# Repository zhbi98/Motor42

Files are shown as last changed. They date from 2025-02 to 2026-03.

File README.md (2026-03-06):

# Motor42

转速-扭矩特性步进电机运用普通的开环控制方式在低速和低负载的情况下可以保持较好的控制精度，但随着负载增大或转速度增加会发生丢步，另一个是转速-扭矩特性让步进电机无法在高转速下稳定工作。

## 特性

在低速状态下，步进电机的扭矩特性曲线通常为水平直线，能够提供较高的扭矩。在高速状态下，由于电感的影响，扭矩特性曲线呈指数下降，导致电机的负载能力显著降低。

> **最大扭矩：** 最大扭矩出现在中低转速范围，随着转速的提高，扭矩会逐渐下降。因为在高频率下，电流流动受到绕组电感的影响，导致电流无法达到稳定值，从而扭矩降低。
> 
> **启动扭矩与连续扭矩：** 启动扭矩指在启动时能够提供的最大扭矩，而连续扭矩则指电机持续运行时能够维持的扭矩。随着脉冲频率的增加，启动扭矩和连续扭矩都会下降。

## 闭环

闭环控制是在开环控制的基础上，增加了 **反馈检测环节**（例如在电机轴增加编码器），形成指令-执行-位置检测-修正的闭环逻辑。解决存在的丢步、偏差、抗干扰能力弱问题，还能提升系统和容错能力。

## FOC 控制

混合式步进电机与无刷电机的内在联系（结构定义相似性，工作原理相似性），所以可以用无刷电机 FOC 的驱动思想驱动步进电机。

结构方面：永磁转子+定子绕组的结构，定子方面：两者都有多相绕组（步进电机通常为两相，无刷电机通常为三相），转子方面：都采用永磁材料制造转子磁极，无刷设计：两者都没有电刷和机械换向器，依靠电子换向。

对于两相步进电机，虽然只有两个绕组，但通常两相绕组是正交的，从而可以简化步骤，省略我们的 clarke 变换，所以其余同样可以采用类似的思路进行一个电流环FOC控制。

    电流检测：对 AB 两相电流进行检测
    Park变换：将 AB 轴静止系转换为dq轴旋转坐标系
    PI调节器：对 Id 和 Iq 进行控制
    Invpark变换：讲 dq 轴转换为AB轴
    SVPWM调制: 输出占空比
    双 H桥驱动：驱动我们的步进电机

这些可以整合到一个驱动器中实现，如下图。这就是一体化集成步进电机闭环驱动器。板上集成磁编码器，具有速度，位置，电流闭环控制功能，适用于 3D 打印机，小型机械臂。

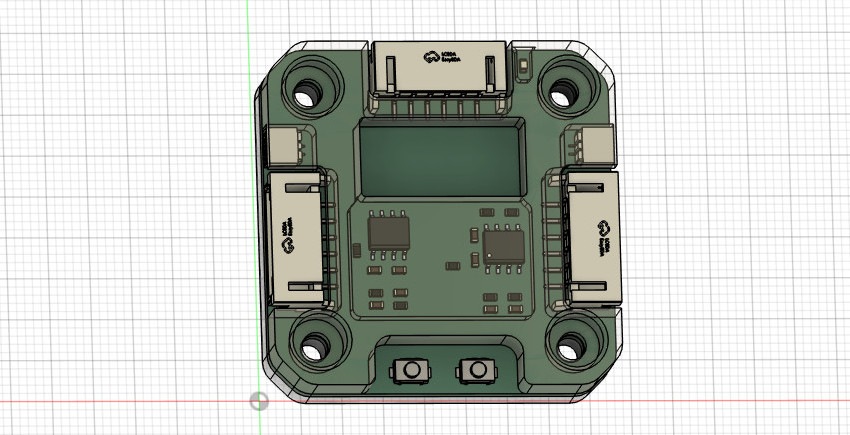
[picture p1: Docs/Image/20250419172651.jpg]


## 硬件

(1) 2 相逆变功率级：东芝凌耐压 50V，载流3.5A 的 PWM 斩波式双全桥电机驱动器，内置带低导通电阻的输出MOSFET（基于成本考虑可以选择其他的型号）。

(2) RS485 收发器：TI 德州仪器 SN75176B（基于成本考虑可以选择其他的型号）。

(3) CAN2.0B 收发器：NXP 恩智浦 High-speed CAN transceiver TJA1051（基于成本考虑可以选择其他的型号）。

(4) 磁编码器：MagnTek 麦歌恩 mt6816 单圈绝对式14位编码器，支持最高转速25Krpm。

(6) 主控 MUC 芯片：意法半导体 STM32F103。

## 关于打样

驱动器板 Motor42（PCB 采用?**4 层板**?设计）：[HardWare/kiacd_project](./HardWare/kiacd_project)

如果想自己修改 PCB 需要安装 KiCad（开源的 EDA 工具，也非常易学），官方下载地址： https://www.kicad.org/。

打样制作可以直接进入到下面这两个路径下：

把 Motor42 Gerber 文件夹 [HardWare/Gerber](./Docs/Motor42-PCB/) 压缩为 Motor42.zip，

把这个 .zip 给 PCB 制造厂即可（例如 JLC，**PCB 经过打样验证，可以放心使用**）。

**器件 BOM 目录**：[HardWare/ibom.html](./Docs/Motor42-BOM.csv)（PCB 没器件位号，按网页交互式 BOM 贴片）。

原理图 PDF 目录： [Docs/Motor42-SCH.csv](Docs/Motor42-SCH.pdf)

## 核心固件

固件主要包括几大功能模块：

- hal 驱动：板载的各种硬件驱动比如 USB、Tim、Can、Spi。
- utils 库：STM32 的 Flash 存储接口，Modbus 协议解析库，软定时器组件。
- drivers：ARM的CMSIS驱动，ST官方的HAL库。
- device：电机H桥驱动，编码器驱动和校准，电机控制核心代码，LED 驱动框架 LedMX 和按键驱动 MultiButton。
- main：上层 Can，Rs485 应用控制协议，用于控制同步电机状态/参数，以及用户设置参数保存功能。

## 编译下载

固件没有使用 ARM Keil 开发，而是先用 CMake 构建出 Makefile，然后再用 arm-gcc 编译（可以自己创建 F103 的 Keil 工程，把 Motor42 组织到 Keil 编译）。

Motor42 用的是 VSCode 搭配 OpenOCD 图形化下载调试，需要下载安装下列工具链：

MiniGW： https://sourceforge.net/projects/mingw-w64/files/

arm-gcc ：[Downloads | GNU Arm Embedded Toolchain Downloads – Arm Developer](https://developer.arm.com/downloads/-/gnu-rm)

openOCD：[Download OpenOCD for Windows](https://gnutoolchains.com/arm-eabi/openocd/)

CMake：[Download CMake](https://cmake.org/download/)

VSCode：[https://code.visualstudio.com/](https://code.visualstudio.com/)

> 安装后具体如何配置使用这些工具，篇幅较长不写在这里，我把具体配置使用方法写在这里：[工具链配置使用方法](https://blog.csdn.net/jf_52001760/article/details/126826393)。

**Motor42 编译步骤**：

把 cmake 脚本 CMakeLists.txt 的目录添加到 `1` 这里，如下图。

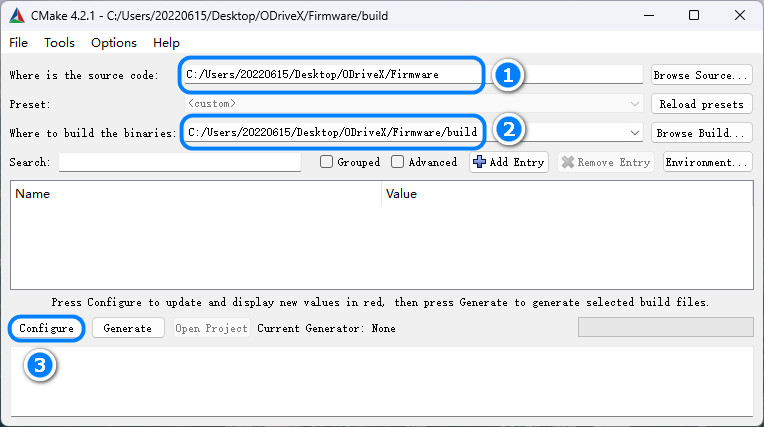
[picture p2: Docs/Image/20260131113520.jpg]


(2) 在 Firmware 目录下创建 build 目录，并指定到 `2` 这里。

(3) 点击 "Configure"，在弹出面板选择目标工程，如下图。

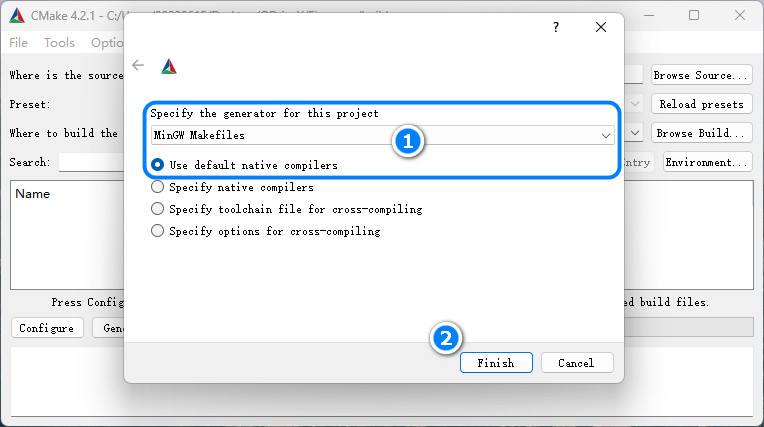
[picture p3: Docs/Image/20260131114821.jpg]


(5) 在 vscode 的命令行 `cd build` 进入`build/`目录，然后执行 make -j2 即可开始编译。

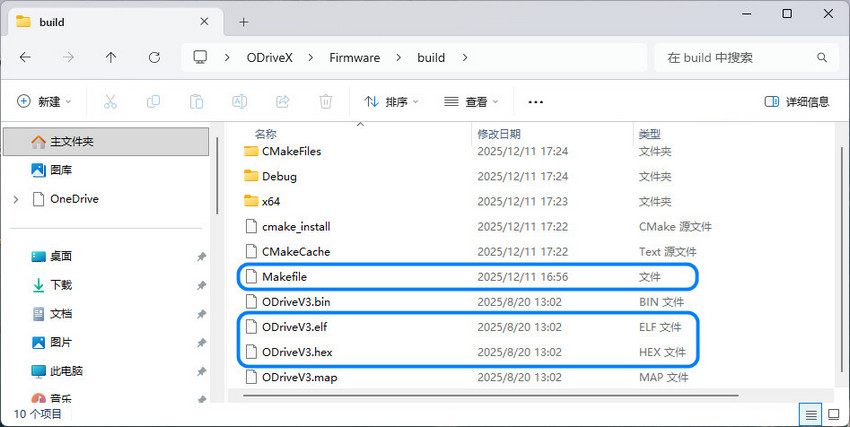
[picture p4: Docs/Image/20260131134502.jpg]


(6) 使用 openOCD 把 `.elf` 文件下载到 Motor42 硬件，下载方法同样参照 [工具链配置使用方法](https://blog.csdn.net/jf_52001760/article/details/126826393)（PCB 上预留了 SWD 调试接口同时支持固件下载）。

## 电机选型

电机可以在淘宝搜索购买，最好购买低相电阻步进电机（较好的电机的相电阻通常为 2-5 Ohm）。相电阻过高可能导致电机在静止时出现高频震动。

电机机身：34MM，出轴直径：5MM (D轴4.5MM)，出轴长度：22MM
静力矩：0.29 N.m，额定电流：1.5 A，电阻：3.0Ohm/相。

> 要实际测量电机相电阻（万用表接到对应相的两个端子测量），比如购买的步进电机在参数描述中标明的相电阻为 2.2 Ohm，实则实际测出的相电阻高达 29 Ohm
> 
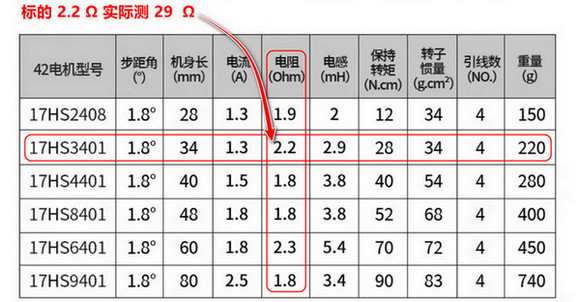
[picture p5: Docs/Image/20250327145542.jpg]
> 

## 编码器安装

在电机轴上安装径向磁铁（用于磁编码器检测），磁铁尺寸?$d=8mm$，$h=2mm$，注意径向磁铁和轴同心度不要过度偏移，让后把驱动器板放到板支架中，用 M3.0 螺丝把驱动器和板定到电机尾部，磁铁与编码器的间隙大概为 $1mm$。

驱动板支架零件目录：[Model](./Model)，把 .step 文件给 3D 打印即可。

## Configuration

固件上已经调试好 Pid 参数，可以适配大多数42步进电机，默认情况下不需要再调试 Pid 电机也能正常工作。Pid 可以用 Can 指令调整（看Can协议部分的说明），方法如下：

- **Kp 的调整**：将 Kd，Ki 置 0，从零开始逐渐增加 Kp，直到系统出现震荡。然后逐渐减小Kp，直到系统不再震荡。Kp 的最终值通常在引起震荡的 Kp 值的 80%-90% 之间。

- **Kd 的调整**：在 Kp 调整稳定后，开始增加 Kd。如果系统在空载时仅需要 Kp，那么在负载情况下可能需要增加 Kd 来减少超调和震荡。

- **Ki 的调整**：如果系统在 Kp 和 Kd 的调整后仍然存在静态误差，可以尝试增加 Ki。但 Ki的值通常很小，需要细致地调整。

配置限制参数，限制参数再 /motor/control_config.h 文件定义，如下。

```c
/********************  硬件配置区  ********************/
#define _Current_Rated_Current  (3000)  /**< 额定电流(mA)*/
#define _Current_Cali_Current   (2000)  /**< 校准电流(mA)*/
/********************  运动参数配置区  ********************/
...
#define _Move_Rated_Speed           ((int32_t)(50 * Move_Pulse_NUM))    /**< (额定转速)(50转每秒)*/
#define _Move_Rated_UpAcc           ((int32_t)(1000 * Move_Pulse_NUM))  /**< (固件额定加速加速度)(1000r/ss)*/
#define _Move_Rated_DownAcc         ((int32_t)(1000 * Move_Pulse_NUM))  /**(固件额定减速加速度)(1000r/ss)*/
#define _Move_Rated_UpCurrentRate   ((int32_t)(20 * _Current_Rated_Current))    /**< (固件额定增流梯度)(20倍额定/s)*/
#define _Move_Rated_DownCurrentRate ((int32_t)(20 * _Current_Rated_Current))    /**< (固件额定减流梯度)(20倍额定/s)*/
```

用户设置在 /main/setup/setup.c 中定义，用户设置参数可以用 Can 指令设置（看Can协议部分的说明）设置后保存在 Flash 掉电保存。

```c
const _setup_t _setup_def = {
    ...
    .can_id = 0x01,
    .home_ofs = 0,
    ...
    .current_down_acc = 2 * 1000, /*(mA/s)*/
    .current_up_acc = 2 * 1000, /*(mA/s)*/
    .current_rated = 1000,
    .cali_current = 2000,
    ...
};
```

## 按键逻辑

(1) 启动停止闭环模式：按键 1 短按一次，启动或停止闭环模式，启动闭环模式的同时会进入默认的模式，例如位置闭环。

(2) 目标清 0：按键 2 短按一次，如果当前控制模式为速度模式，那么按下此时会将目标速度置为 0，位置模式，则将目标位置置为 0。

(3) 电机编码器校准：按键 1 长按两次，校准时电机会慢速正转一圈再反转一圈。

> 按下按键时 LED 跟随闪烁，以指示按键是否响应。

## 通信协议

驱动器支持 RS485+Modbus 和 CAN 协议。

### CAN 协议

一帧 CAN 报文只能传 8 个字节数据，和 11 位的标准 Std-Id，这里把 Std-Id 的低 7 位也用作数据，用来传控制指令字 CMD，控制协议定义如下：



Device Id 占用 4 位，CMD 占用 7 位，协议最多两个参数：参数 1 占用 4 个字节，参数 2 占用 4 个字节。

> 个别协议要两个参数，例如位置控制：设置目标位置和速度限制。

具体指令在[protocols/can_protocol.c](./Firmware/main/protocols/can_protocol.c) 这里定义，具体可以看这个文件，具体控制指令和控制方式查看 [Docs/Protocols](./Docs/Protocols) 目录下相应的协议文档，这里只截取部分。

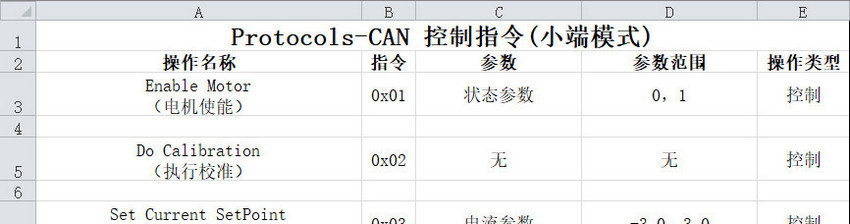
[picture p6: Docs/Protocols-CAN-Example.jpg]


### Rs485 协议

具体控制指令和控制方式查看 [Docs/Protocols](./Docs/Protocols) 目录下相应的协议文档，这里只截取部分。

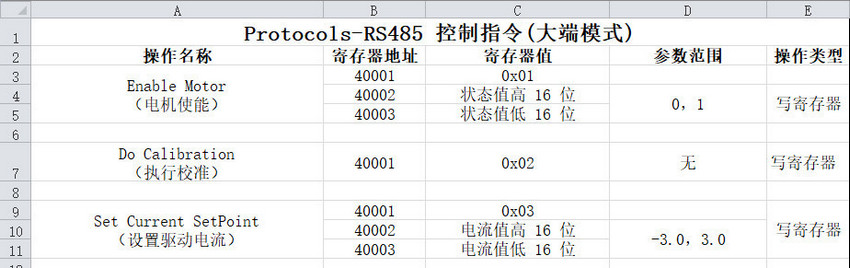
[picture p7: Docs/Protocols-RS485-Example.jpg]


## 震动问题

注意步进驱动器控制步进电机工作在位置环并要求静止在某个固定位置时可能会出现高频震动的问题。引起高频微弱震动的原因是由于在位置环控制模式下，驱动器为了让让电机接近指定位置而控制电机在齿槽间反复微调而产生震动。

> 这个现象排除驱动器的电路问题（比如焊接的电流采样电阻是否正确等等），磁编码器检测磁铁的安装同心度问题（通常同心度要求不是很高，确保不要过度偏移即可）那有极大的可能是步进电机的相电阻过大导致的，可以更换了其他电机进行测试。

如果更换电机测试后发现同一个闭环步进电机驱动器驱动一个步进电机工作在位置环保持静止时工作正常，而驱动另一个步进电机静止时出现高频震动，那可以肯定就是相电阻过高而导致的。出现震动现象的电机相电阻通常为 10-30 Ohm，而较好电机的相电阻通常为 2-5 Ohm。注意检查电机参数可能的虚标，例如购买的步进电机在参数描述中标明的相电阻为 2.2 Ohm，实则实际测出的相电阻高达 29 Ohm，所以电机出现震动现象和线圈相电阻是有一定关系的。

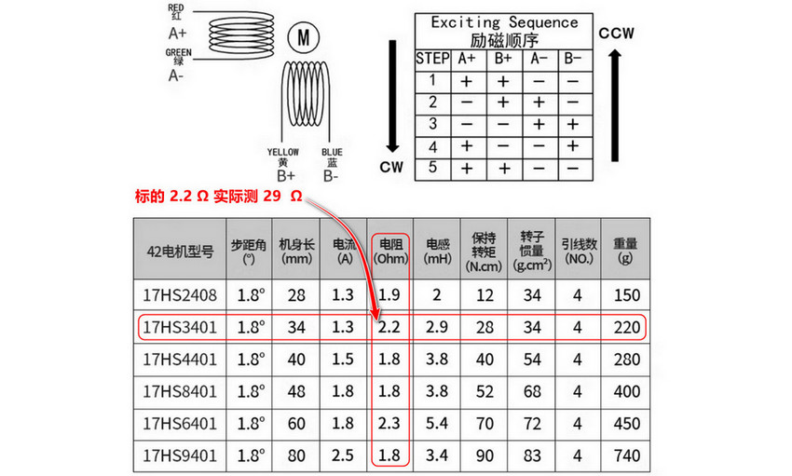
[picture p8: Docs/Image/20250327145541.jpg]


可以通过修改驱动器程序固件来修复这个问题，修改驱动输出部分，在最终 FOC 输出驱动电流部分添加一个系数即可，通过该系数来调节驱动器 FOC 的输出电流（当然调节电流参数会对最终的扭矩有略微的影响，但并不影响闭环精度），如下图。

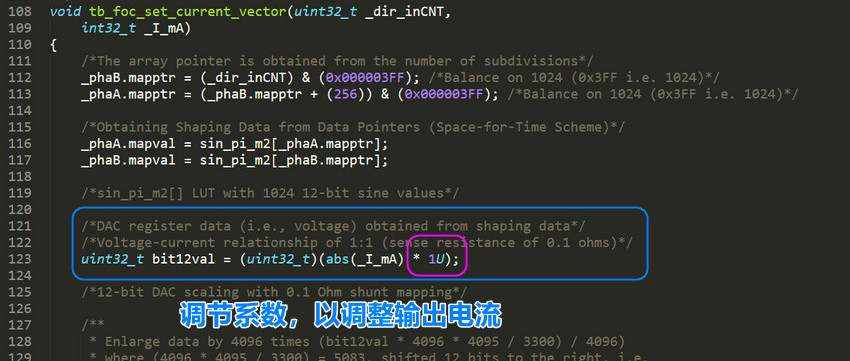
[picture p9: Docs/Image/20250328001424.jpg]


## 控制带宽

电机控制速度/位置积分需要精确节拍，电机控制所有逻辑都是在定时器触发的中断中进行，我设置的中断函数频率较高，达到20KHz，可能会导致 main 主循环不执行。

> **20 kHz 中断**：TIM 每 50 μs 触发一次中断。

**电机控制逻辑较多：** 运行时间合计接近或超过 50 μs，会形成中断几乎连轴转、主循环几乎没机会跑”的情况（和芯片主频无关，只要中断内处理的时间超过中断周期时间就会导致 main 函数不执行）。

> 通过 SPI 阻塞读 MT6816，最多 3 次尝试 × 2 次 16bit 传输，再加 16 位奇偶校验循环。SPI 时钟为 9MHz，仅通信就可能 5-15μs。
> 
> 编码器处理、位置/速度估计、多种运行模式下的控制（DCE/PID/电流等）、运动规划、软目标更新、堵转/过载检测等就需要数十μs。

没有具体要求需要多少控制频率，控制制带宽越高，控制越平滑所以默认设定为 20KHz，若控制带宽允许，可把闭环控制改为 10 kHz 或 5 kHz，中断周期变为 100 μs / 200 μs。

> 这里 20 kHz 不是控制带宽的硬性要求，更多是裕量和步进分辨率。

修改控制频率同时改两处：
motion_planner.h 的  CONTROL_FREQUENCY 定义。
修改电机控制运行中断定时器的中断时间。

```c
/****************************************  控制器频率配置区  ****************************************/
#define CONTROL_FREQ_HZ   (20000)                     /**< 控制频率_hz*/
#define CONTROL_PERIOD_US (1000000 / CONTROL_FREQ_HZ) /**< 控制周期_us*/
```

### 评估控制带宽

(1) motor.cpp 涉及的一阶滤波：由 `等效时间常数由 >> 5`（约 32 个采样）决定。20 kHz 时：32 × 50us =1.6 ms 即控制带宽约 100 Hz。对很多应用来说 50 Hz 左右就足够。

(2) 位置/速度环 (DCE、PID 闭环带宽)：这是外环（位置环、速度环），一般做到几十到一两百 Hz 带宽就足够（位置/速度环 -3 dB 带宽）。 

> 常见经验：**采样率 ≥ 10～20 倍闭环带宽**。 
> 若你目标闭环带宽在 100～200 Hz，**5 kHz 已经够用，2 kHz 是底线**。

(3) FOC/电流指令：由 TB67H450 等驱动接收，5～10 kHz 更新电流给定对多数应用足够。

(4) 运动规划：用 CONTROL_FREQUENCY 做离散积分，频率高一点更平滑，但 5～10 kHz 通常足够平滑。

(5) 控制更新频率：下限约 2～5 kHz（再低速度估计和环路的相位裕量会变差）。推荐 5～10 kHz 在保证控制性能的同时，能给主循环留出明显时间。在需要 **极高步进率** 或 **尽量小的相位延迟** 时才必要 20 kHz。

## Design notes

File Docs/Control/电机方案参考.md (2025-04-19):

# 闭环硬件方案

https://blog.csdn.net/weixin_44746581/article/details/109462132

https://blog.csdn.net/xztli/article/details/127179256

https://blog.csdn.net/weixin_47407066/article/details/124657473

https://blog.csdn.net/BadBoyHolly/article/details/108186896

http://szdelco.com/jszx/jszx_162.html

https://www.elecfans.com/d/781462.html

## TB67H450 驱动芯片

https://blog.csdn.net/Alin_13/article/details/127492569

https://www.ewbang.com/community/article/details/961181993.html

https://blog.csdn.net/Keitheasun/article/details/127779580

https://blog.csdn.net/qq_44897194/article/details/105524808

https://zhuanlan.zhihu.com/p/352785322

https://www.cnblogs.com/huayizi/p/12066665.html

## MT6816 磁编码芯片

https://blog.csdn.net/Keitheasun/article/details/127597480

https://blog.csdn.net/gjy_skyblue/article/details/127049382

https://blog.csdn.net/Mark_md/article/details/126910658

https://www.pudn.com/news/635e3c1ca4b7e43a5ee3e1ca.html

http://www.midlle.com/news/xpfb364.html

https://www.bilibili.com/video/BV1Xf4y127Wd/?spm_id_from=333.788.recommend_more_video.-1

https://blog.csdn.net/weixin_43234123/article/details/125369022

https://blog.csdn.net/raulcy/article/details/127213434

## 径向磁铁

使用径向磁铁，磁力线沿半径方向走的磁铁叫径向磁铁。

一般是圆环形，圆环外面是一个磁极，里面是另一个磁极。

## 测速方法

https://blog.csdn.net/Roger_717/article/details/123410231

https://zhuanlan.zhihu.com/p/104327562

https://blog.csdn.net/hzh68128387/article/details/113433495

## 其他

STM32F103CBT6 不支持 USART0

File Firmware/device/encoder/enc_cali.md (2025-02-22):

`_enc_cali_tick_work` 校准原理

校准的原理是利用前面采集到的 200 个数据（每 1.8° 采集一个数据)，进行线性插值处理，将 200 个数据插值到 16384 个数据（而插值后的数据范围为 0-512000，即 256 * 200 = 512000，就是步进电机单圈脉冲数），这样磁编码器量程范围内的每个编码值都有一个插值数据与之对应，校准后利用磁编码器编码值作为作为插值数据数组下标查表得出校准值即可。最终的思想就是获取磁编码器的读数再查表就可以知道步进电机的位置是多少个脉冲。

`_enc_cali_verify` 寻找阶跃值作用

寻找区间下标及阶跃差值，用于寻找电机开始位置，因为电机不一定从 0 位置开始采集数据，通过循环的方式依次比较相邻两个数据的插值以寻找前面采集到的 200 个磁编码值数据中的数据阶跃值，与阶跃位置。需要寻找阶跃值的原因是，在校准数据采集阶段，采集开始时电机轴所处的位置不一定为 0，即磁编码值不为 0 我们也没有将电机驱动到 0 处再开始采集。所以采集到的磁编码器数据不是按照从小到大或从大到小依次排列的，例如排列方式为 [8192, 8193, ..., 16383, 16384, 0, 1, ..., 8190, 8191] 这种排列方式。

`_enc_cali` 校准数据采集流程（共采集 200 个数据）：

注意，电机运行方向不同采集到的数据排列规律不同，所以需要正转数据与反转数据进行计算。

(1) 失能状态：检测是否开启编码器校准流程
(2) 准备正向校准：驱动电机快速顺时针旋转一圈后停止（排除障碍物的干扰），准备采集顺时针旋转产生的角度数据。
(3) 正向测量：电机顺时针慢速转动，每转过 1.8 度采集 16 个角度数据，16 个数据采集完成后计算 16 个数据的平均值作为该点最终的角度数据。
(4) 反向回退：继续顺时针旋转使其达到一圈零 20 步，因为第 (3) 步的正向测量流程会超过一圈，所以干脆凑整，使其超过量凑整为 20 步，凑整后方便下一步消除。
(5) 反向消差：上一个步骤 (4) 产生了一个超位量，该超位量通过当前步骤逆时针驱动电机旋转 20 步以消除。
(6) 反向测量：步骤和正向测量流程相同，仅仅是电机旋转方向改为逆时针驱动。
(7) 解算：关闭校准功能，通过参数计算和存储功能函数解算采集到的 200 个角度数据。

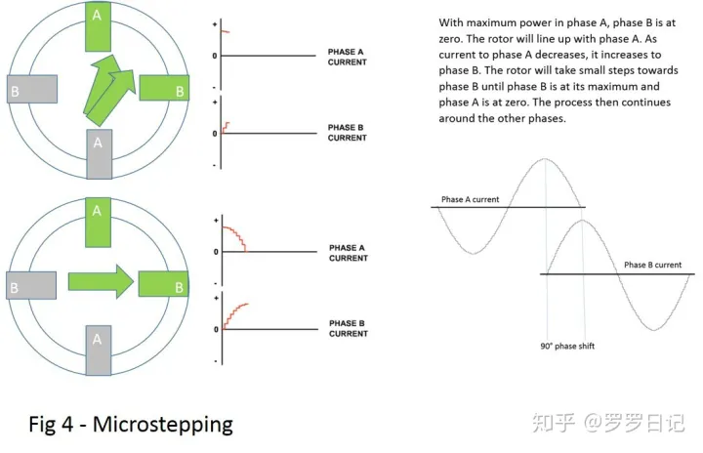
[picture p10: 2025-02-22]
Docs/Control/细分电流波形2.webp

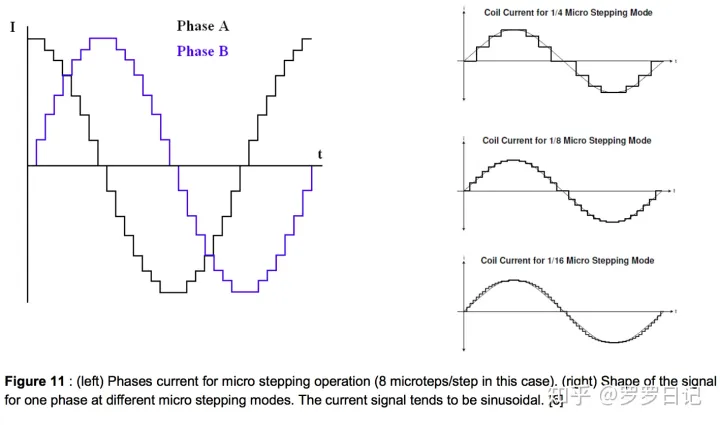
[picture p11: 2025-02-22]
Docs/Control/细分电流波形1.webp

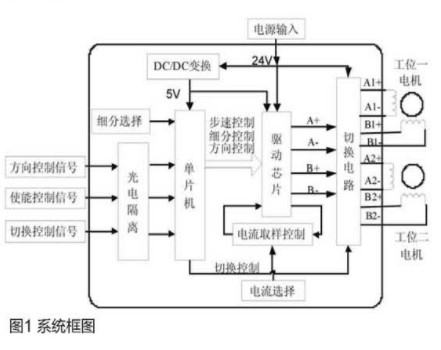
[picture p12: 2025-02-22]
Docs/Control/闭环系统框图.jpg

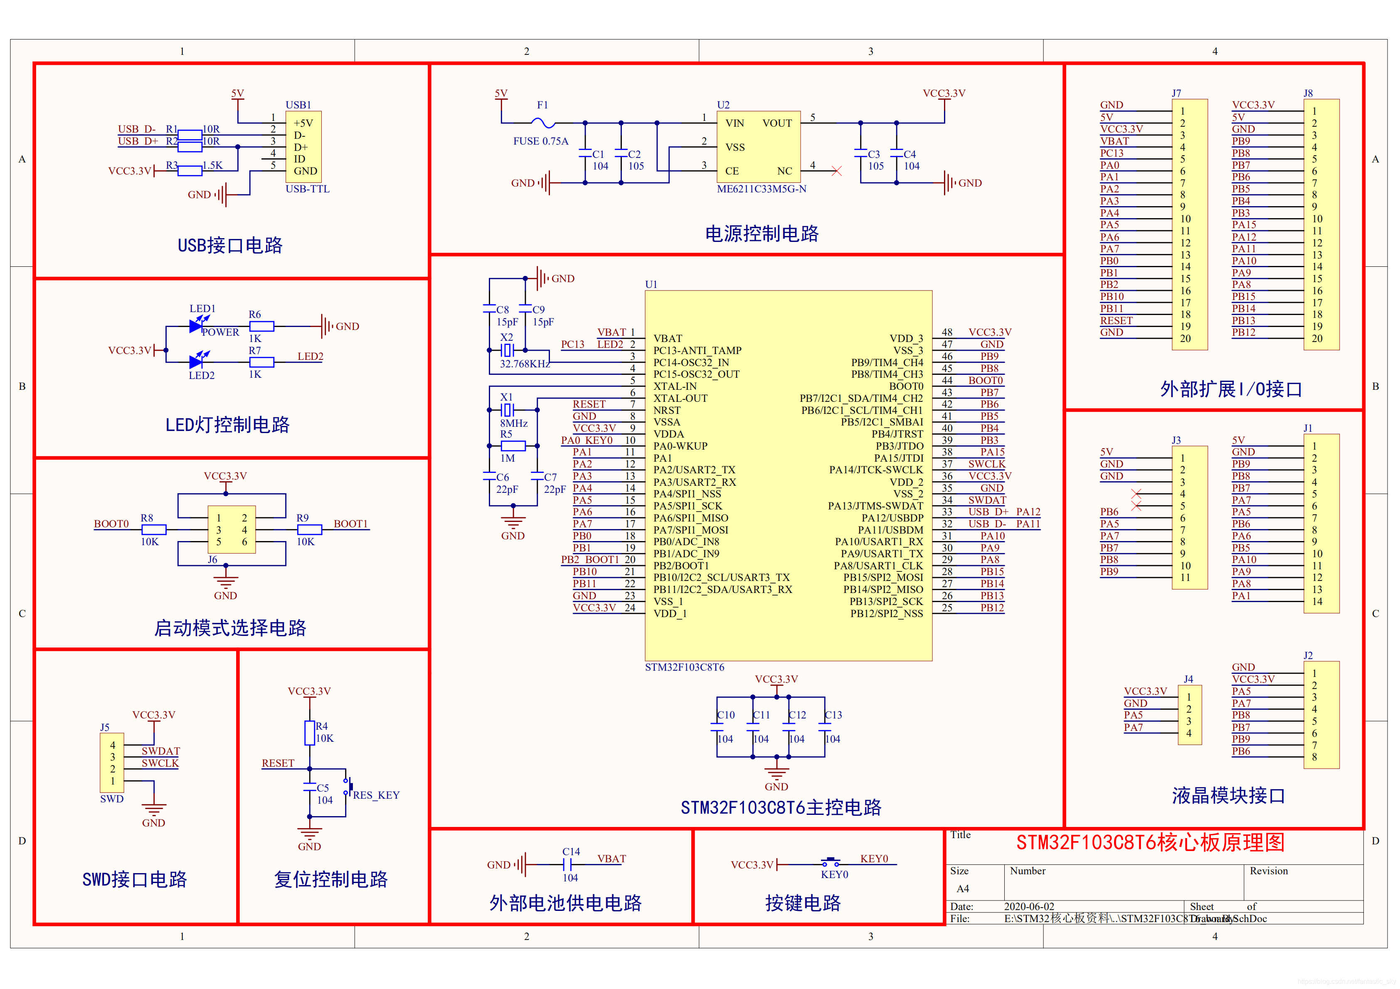
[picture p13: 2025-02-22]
Docs/Arm-STM32/STM32F103C8T6引脚.png

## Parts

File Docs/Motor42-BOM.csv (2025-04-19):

Reference | Value | Datasheet | Footprint | Qty | DNP
C1,C3,C5,C7,C10,C11,C16 | 0.1uF | ~ | Capacitor_SMD:C_0603_1608Metric | 7
C2,C6 | 22pF | ~ | Capacitor_SMD:C_0603_1608Metric | 2
C4,C8,C17,C26,C31,C33 | 10uF | ~ | Capacitor_SMD:C_0603_1608Metric | 6
C12,C13,C14,C15 | 100nF (104) 10% 50V | ~ | Capacitor_SMD:C_0603_1608Metric | 4
C18 | 100pF(101) 50V | ~ | Capacitor_SMD:C_0603_1608Metric | 1
C19,C20 | 100nF(104) 50V | ~ | Capacitor_SMD:C_0603_1608Metric | 2
C21 | 100nF104 | ~ | Capacitor_SMD:C_0603_1608Metric | 1
C22 | 4.7uF(475) 50V | ~ | Capacitor_SMD:C_1206_3216Metric | 1
C23 | 10uF(106) | ~ | Capacitor_SMD:C_0603_1608Metric | 1
C24 | 47uF(106) | ~ | Capacitor_SMD:C_0603_1608Metric | 1
C27,C28,C29,C30,C35 | 100uF 50V | ~ | Capacitor_SMD:C_1206_3216Metric | 5
C32,C34 | 100nF | ~ | Capacitor_SMD:C_0603_1608Metric | 2
D1 | RED LED | ~ | LED_SMD:LED_0603_1608Metric | 1
D2,D3 | B5819WS | http://www.vishay.com/docs/85622/1n914.pdf | Diode_SMD:D_0805_2012Metric | 2
D4 | SS54 | http://www.vishay.com/docs/85622/1n914.pdf | Diode_SMD:D_SMA | 1
D5 | SMBJ28CA | https://www.vishay.com/docs/88301/15ke.pdf | Diode_SMD:D_SMB | 1
D8 | GREEN LED | ~ | LED_SMD:LED_0603_1608Metric | 1
IC1,IC2 | TB67H450FNG,EL | http://toshiba.semicon-storage.com/info/docget.jsp?did=65346&prodName=TB67H450FNG | 3rd_Driver_Motor:SOIC-8_L4.8-W5.8-P1.27_TB67H450FNG | 2
IC3 | MT6816 | http://www.magntek.com.cn/upload/MT6816_Rev.2.0.pdf | 3rd_Sensor_Encoder:SOIC-8_L4.7-W5.8-P1.27_MT6816 | 1
IC4 | ME3116AM6G | https://componentsearchengine.com/Datasheets/1/ME3116AM6G.pdf | 3rd_Converter_DCDC:SOT-23-6_L2.7-W2.2-P0.95_ME3116AM6G | 1
J1 | DBUG |  | 3rd_Connector_JST_SMD:CONN-SMD_1x3P-P1.0-H_WAFER-SH1.0-3PWB | 1
J2 | SWD |  | 3rd_Connector_JST_SMD:CONN-SMD_1x4P-P1.0-H_WAFER-SH1.0-4PWB | 1
J3,J7 | CAN_BUS |  | 3rd_Connector_JST_SMD:CONN-SMD_1x2P-P1.0-H_WAFER-SH1.0-2PWB | 2
J4 | MOTOR |  | 3rd_Connector_JST_SMD:CONN-SMD_1x6P-P2.0-H_WAFER-PH2.0-6PWB | 1
J5,J6 | POWER IN |  | 3rd_Connector_JST_SMD:CONN-SMD_1x6P-P2.0-H_WAFER-PH2.0-6PWB | 2
J8 | RS485 |  | 3rd_Connector_JST_SMD:CONN-SMD_1x2P-P1.0-H_WAFER-SH1.0-2PWB | 1
JP1 | Jump | ~ | Jumper:SolderJumper-2_P1.3mm_Open_RoundedPad1.0x1.5mm | 1
L1 | FCI3216-6R8 6.8uH | ~ | Inductor_SMD:L_1206_3216Metric | 1
Q1 | 8050-Y1 | ~ | Package_TO_SOT_SMD:SOT-23 | 1
R1 | 10M | ~ | Resistor_SMD:R_0603_1608Metric | 1
R2 | 3.3K | ~ | Resistor_SMD:R_0603_1608Metric | 1
R5,R9,R10,TH1 | 10K | ~ | Resistor_SMD:R_0603_1608Metric | 4
R8 | 1k | ~ | Resistor_SMD:R_0603_1608Metric | 1
R11,R12,R13,R14 | 1KΩ (1001) ±1% | ~ | Resistor_SMD:R_0603_1608Metric | 4
R15,R16 | 0.1Ω (R100) ±1% | ~ | Resistor_SMD:R_1206_3216Metric | 2
R17 | 1.91k(1901) | ~ | Resistor_SMD:R_0603_1608Metric | 1
R18 | 10k(1002) | ~ | Resistor_SMD:R_0603_1608Metric | 1
R19 | 1M | ~ | Resistor_SMD:R_0603_1608Metric | 1
R20,R21 | 12K | ~ | Resistor_SMD:R_0603_1608Metric | 2
R22,R25 | 120R | ~ | Resistor_SMD:R_0603_1608Metric | 2
R24 | 220R | ~ | Resistor_SMD:R_0603_1608Metric | 1
S1,S2 | KEY-PB_4P_MIN |  | 3rd_Button_Switch_SMD:KEY-SMD_2P_L4.0-W3.0-V_K2-1807SN-A3DW-06 | 2
TP1 | SCK | ~ | TestPoint:TestPoint_Pad_D1.0mm | 1
TP2 | MISO | ~ | TestPoint:TestPoint_Pad_D1.0mm | 1
TP3 | MOSI | ~ | TestPoint:TestPoint_Pad_D1.0mm | 1
TP6 | +3.3V | ~ | TestPoint:TestPoint_Pad_D1.0mm | 1
TP7 | +24 | ~ | TestPoint:TestPoint_Pad_D1.0mm | 1
TP8 | +5V | ~ | TestPoint:TestPoint_Pad_D1.0mm | 1
TP9 | GND | ~ | TestPoint:TestPoint_Pad_D1.0mm | 1
U1 | XC6206P332MR | https://www.torexsemi.com/file/xc6206/XC6206.pdf | Package_TO_SOT_SMD:SOT-23 | 1
U2 | STM32F103CBTx | https://www.st.com/resource/en/datasheet/stm32f103cb.pdf | Package_QFP:LQFP-48_7x7mm_P0.5mm | 1
U3 | TJA1051T |  | 3rd_Interface_CAN:SOT96_L5.0-W4.0-P1.27_TJA1051 | 1
U4 | SN75176BDR |  | 3rd_Interface_UART:SOIC-8_L5.0-W3.9-P1.27_SN75176BDR | 1
Y1 | 3225 8M 12PF 10PPM | ~ | Crystal:Crystal_SMD_3225-4Pin_3.2x2.5mm | 1

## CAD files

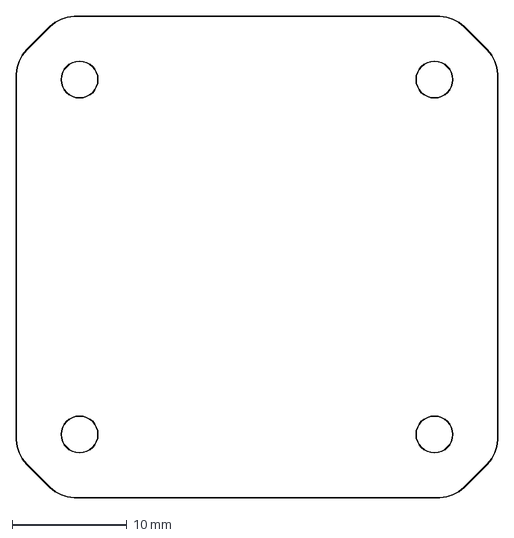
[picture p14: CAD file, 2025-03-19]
HardWare/EDG.dxf
42.0 x 42.0 mm

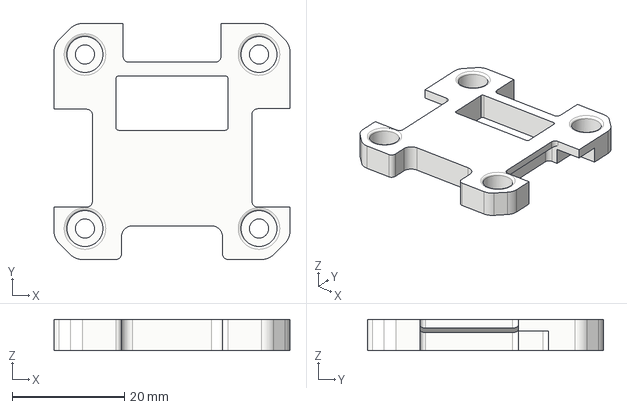
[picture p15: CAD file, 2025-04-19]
Model/Motor42STOP.step
42.0 x 42.0 x 5.55 mm

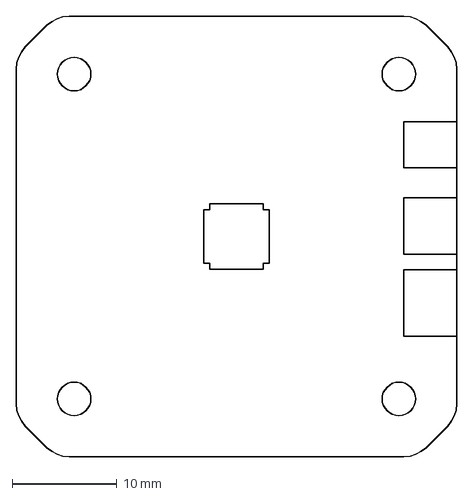
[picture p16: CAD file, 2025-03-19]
HardWare/BOM.dxf
42.0 x 42.0 mm

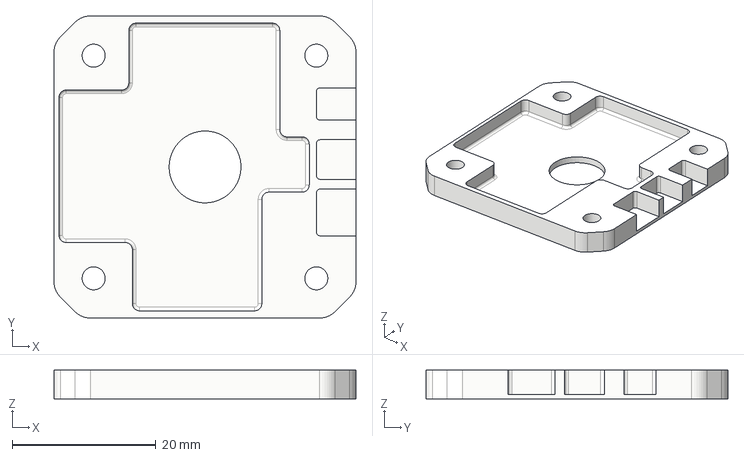
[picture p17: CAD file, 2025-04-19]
Model/Motor42SUP.step
42.0 x 42.0 x 4.00 mm

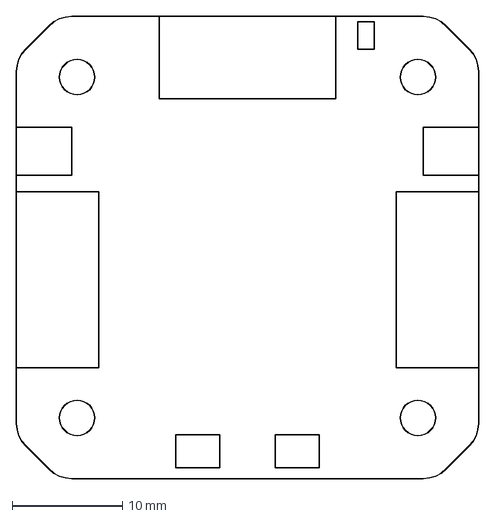
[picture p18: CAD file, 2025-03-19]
HardWare/TOP.dxf
42.0 x 42.0 mm

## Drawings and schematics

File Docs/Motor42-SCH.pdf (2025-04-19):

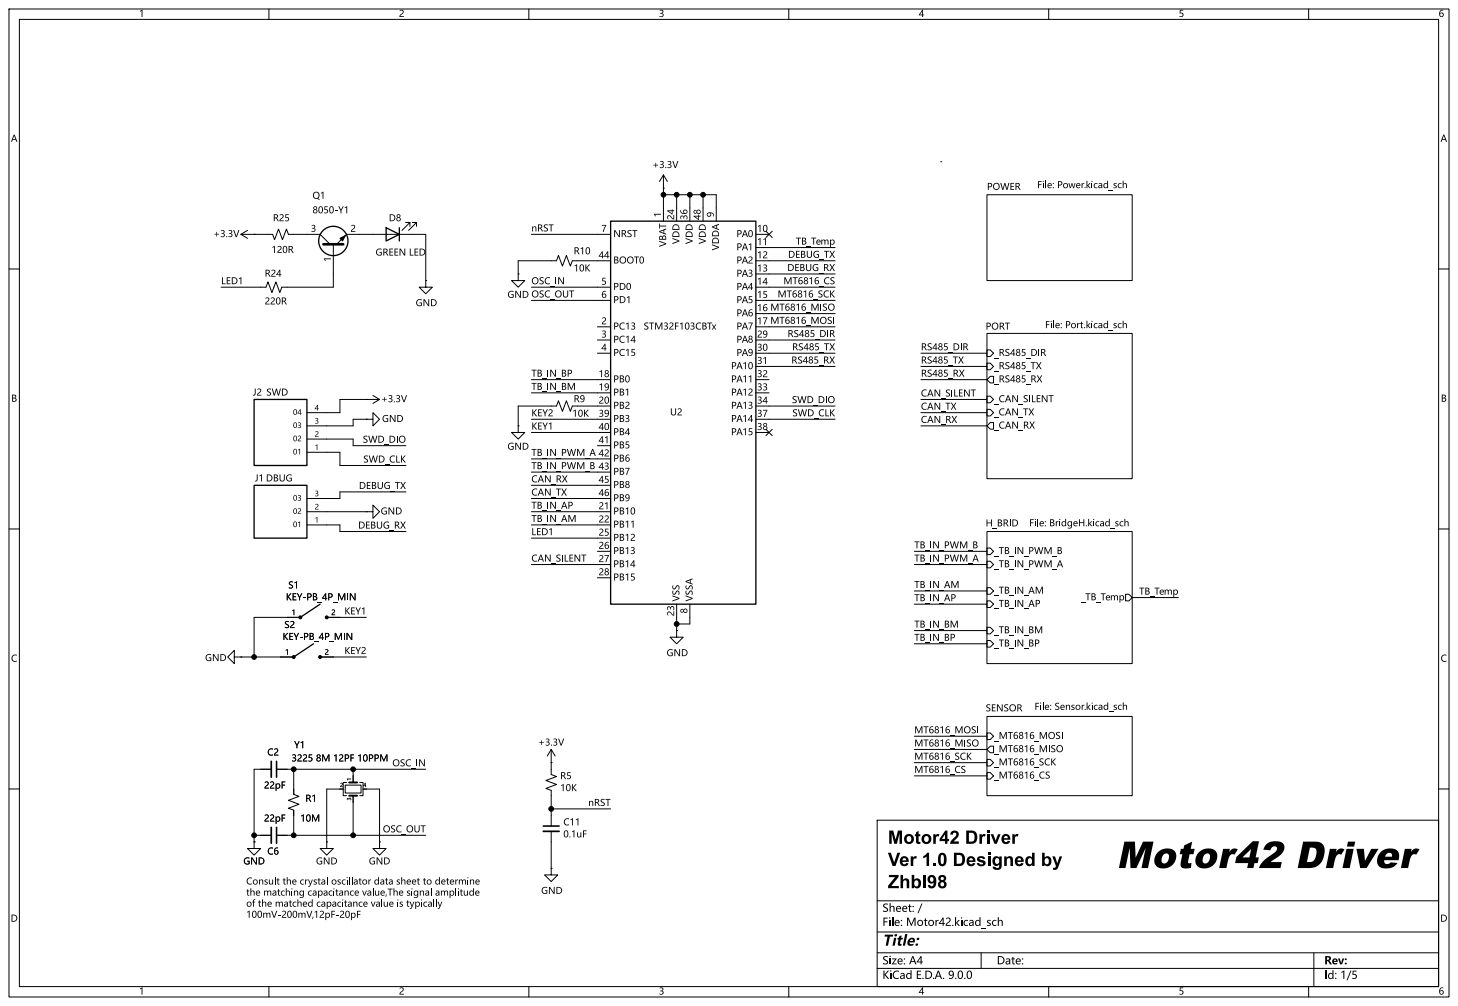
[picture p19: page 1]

1 VDD 24 VSS 23 VDD 36 VSSA

GND
of the matched capacitance value is typically

Id: 1/5 Title: File: Motor42.kicad_sch Sheet: /

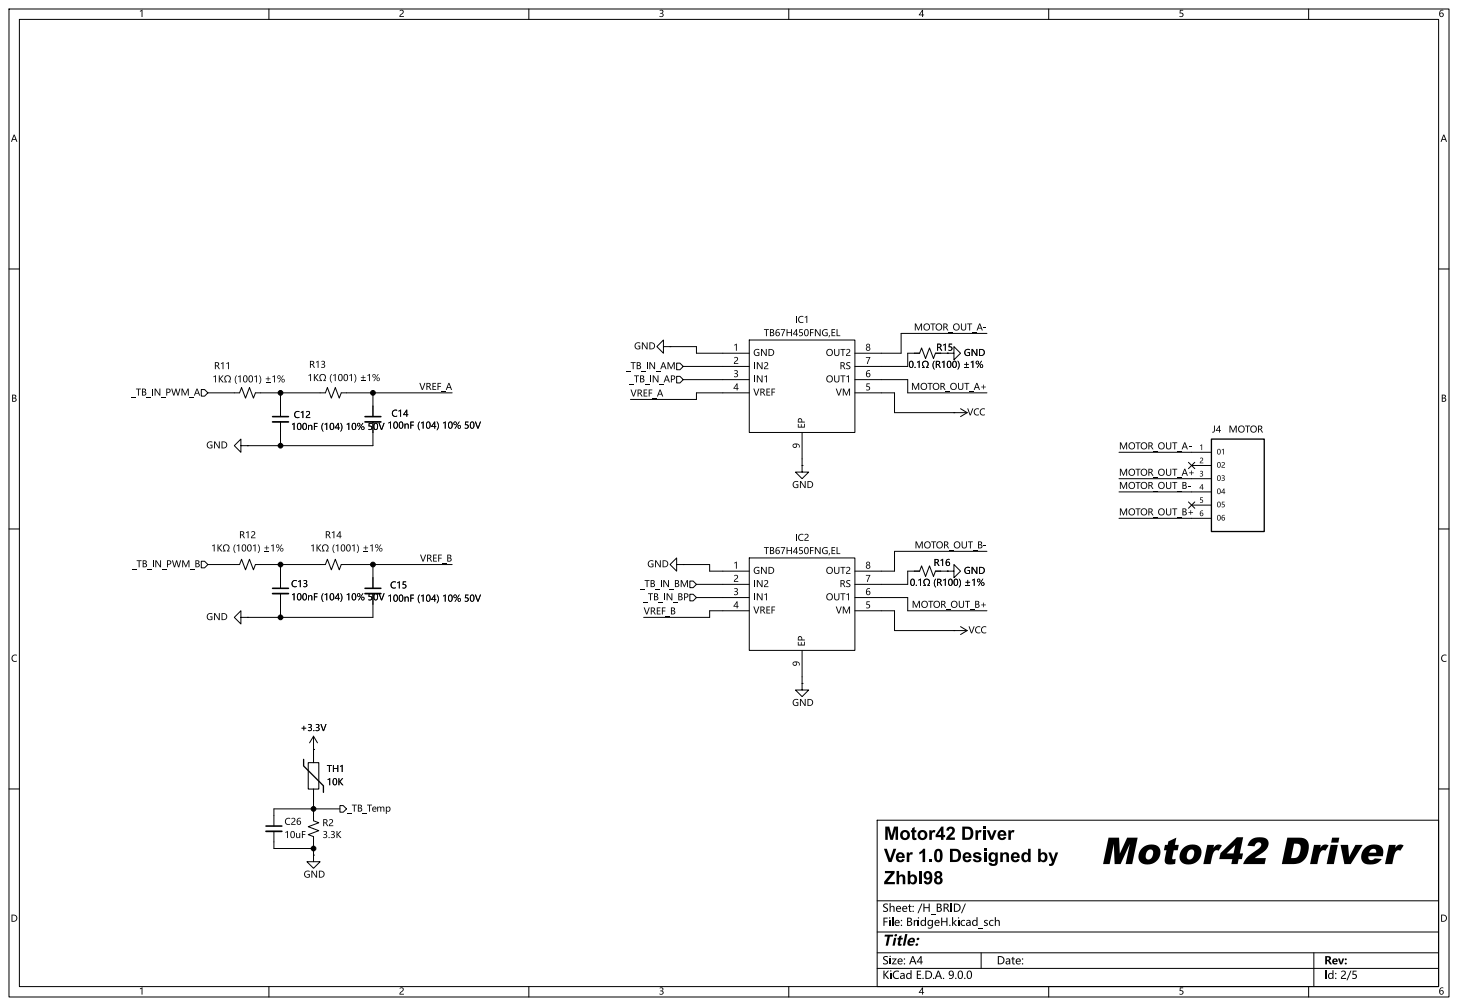
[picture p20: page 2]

Id: 2/5 Title: File: BridgeH.kicad_sch Sheet: /H_BRID/ C13

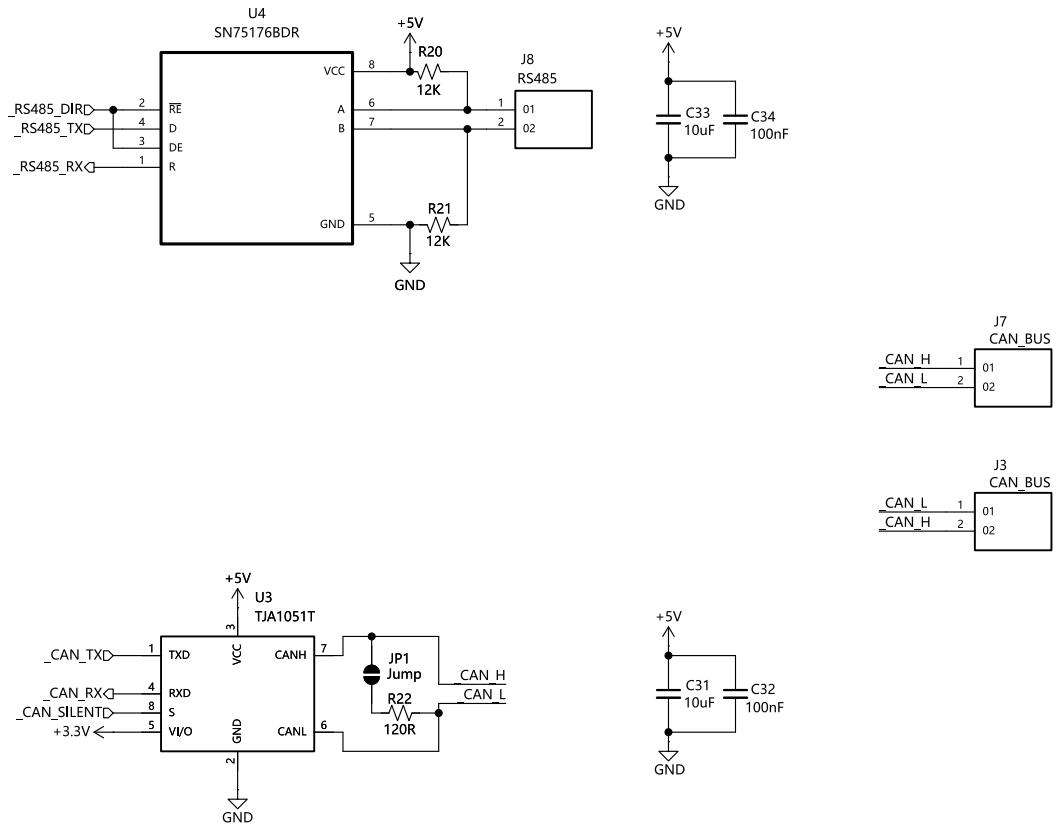
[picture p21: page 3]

Id: 3/5 Title: File: Port.kicad_sch Sheet: /PORT/ JP1
Jump R22

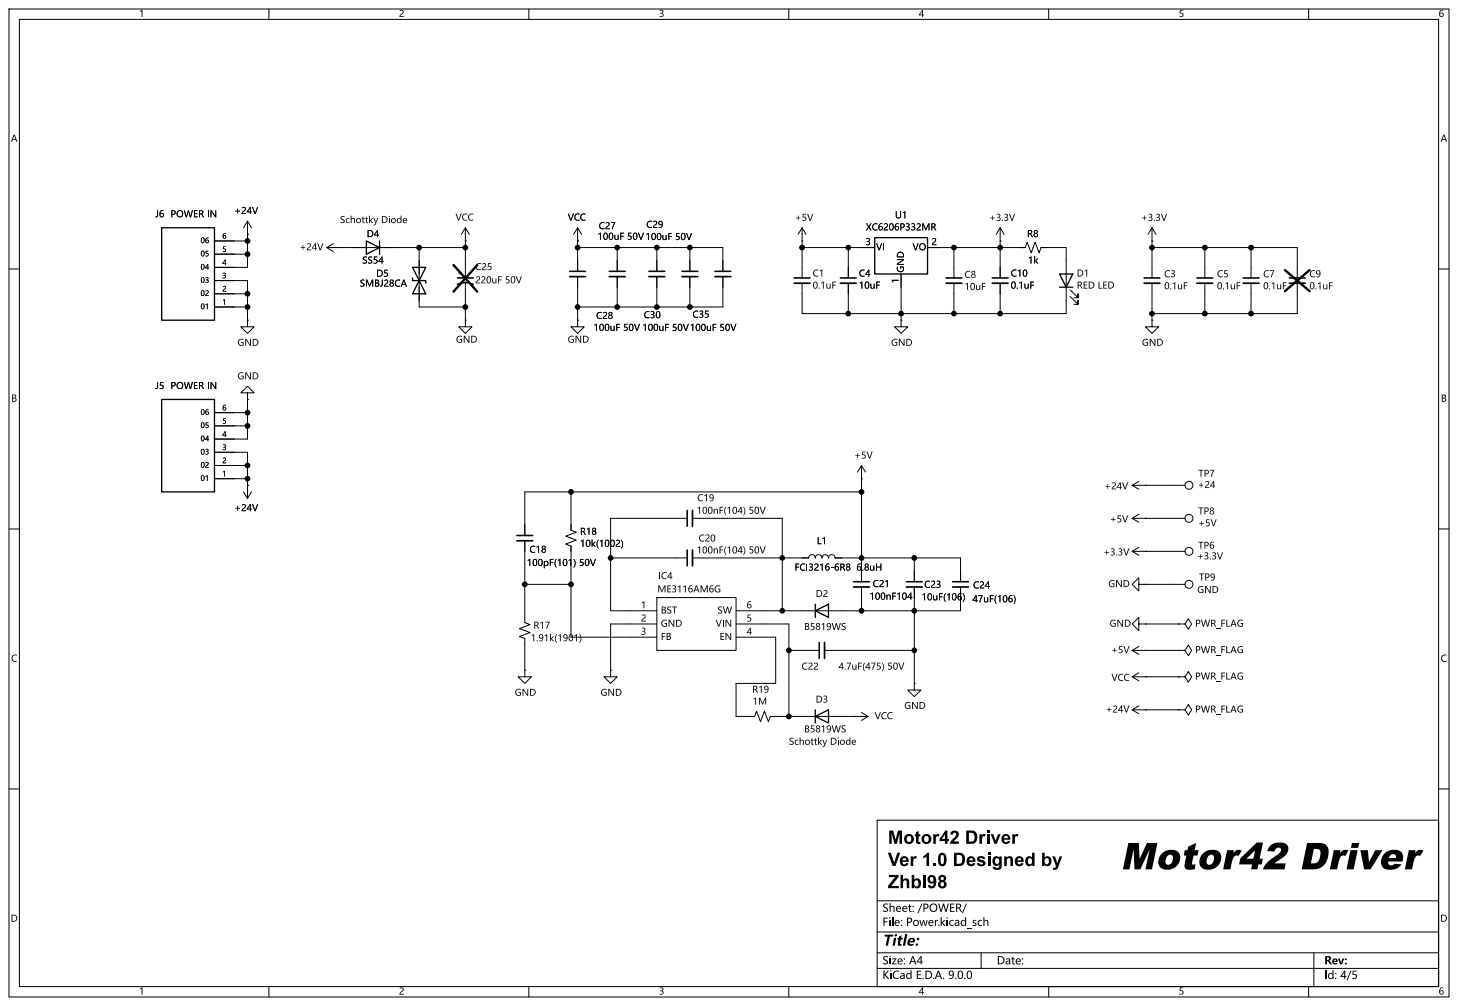
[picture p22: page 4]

Id: 4/5 Title: File: Power.kicad_sch Sheet: /POWER/

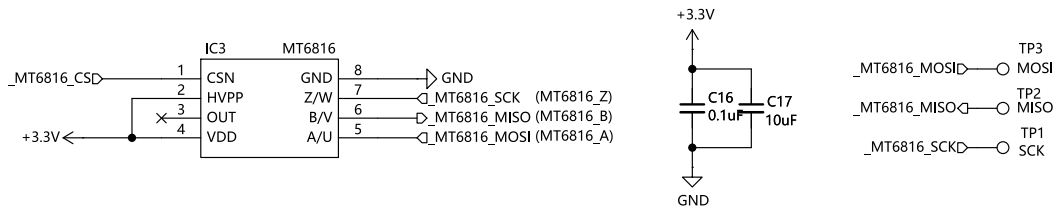
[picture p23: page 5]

Id: 5/5 Title: File: Sensor.kicad_sch Sheet: /SENSOR/

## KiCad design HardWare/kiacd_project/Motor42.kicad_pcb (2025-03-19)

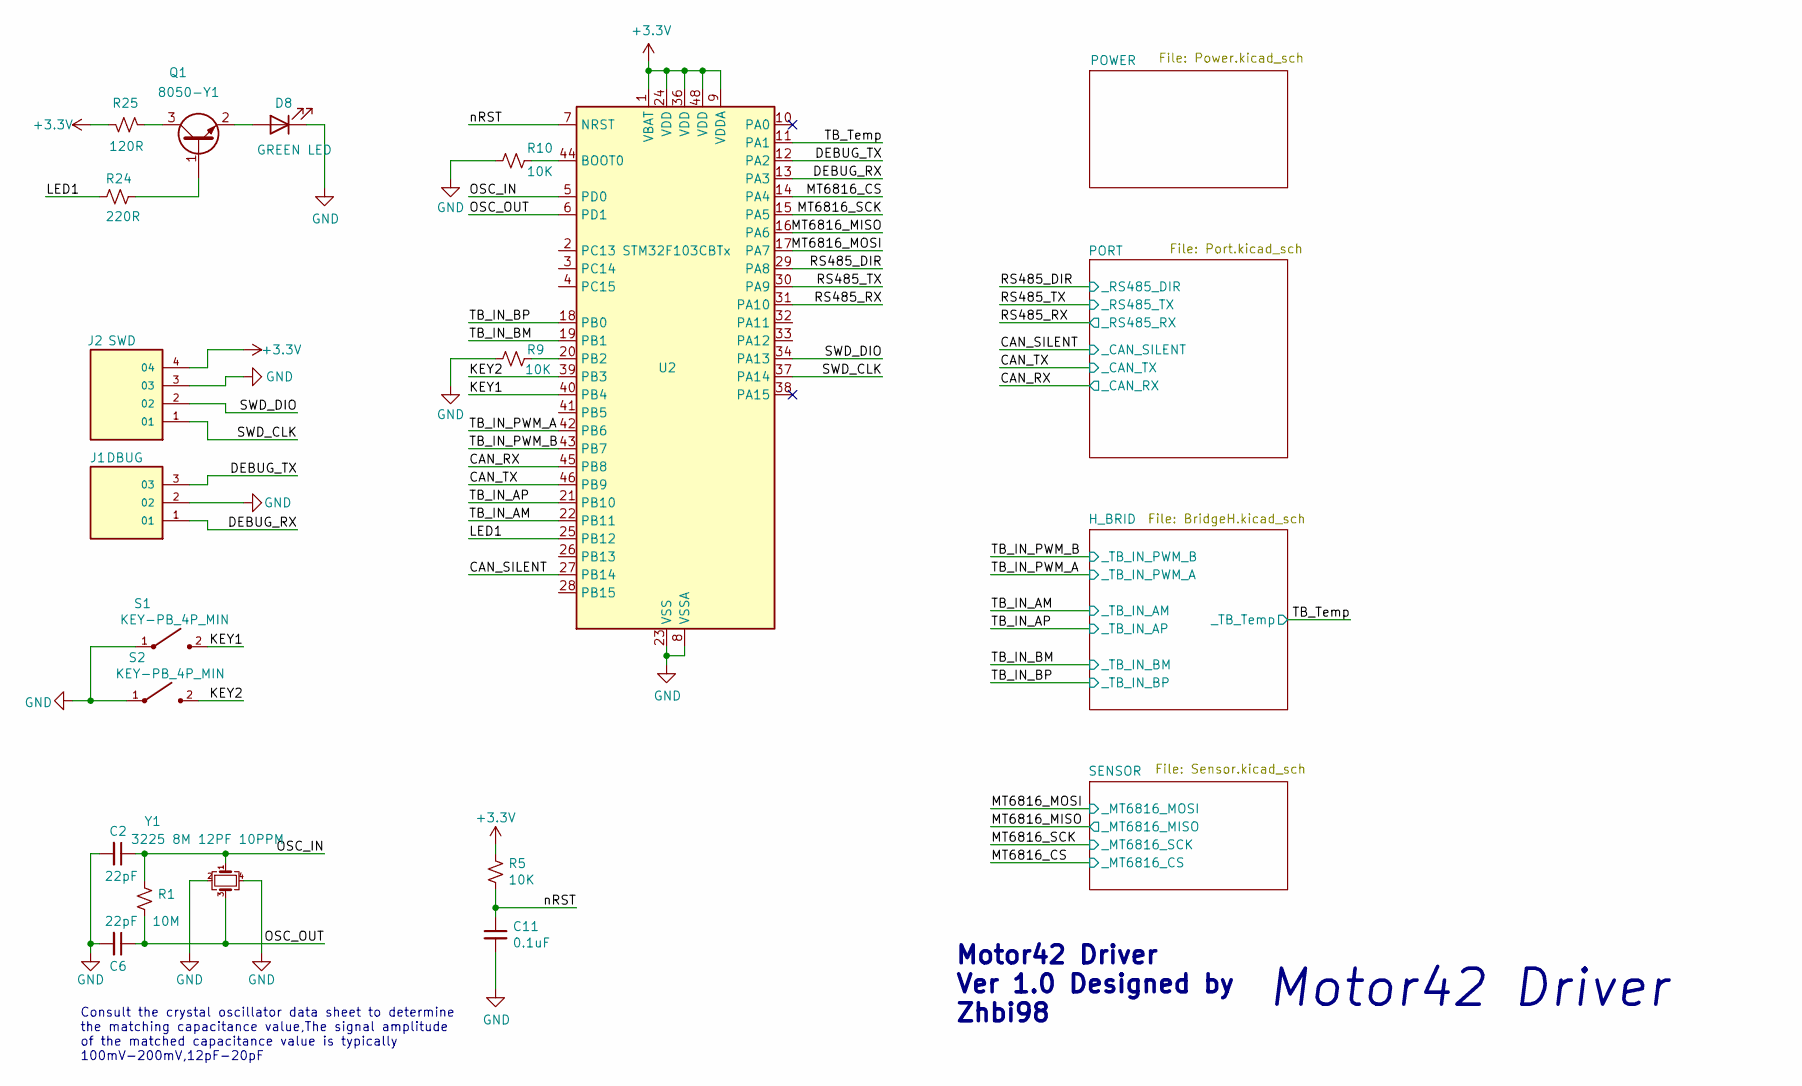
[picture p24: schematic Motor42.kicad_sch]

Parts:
C2, C6: 22pF; C_0603_1608Metric
C11: 0.1uF; C_0603_1608Metric
D8: GREEN LED; LED_0603_1608Metric
J1: DBUG; CONN-SMD_1x3P-P1.0-H_WAFER-SH1.0-3PWB
J2: SWD; CONN-SMD_1x4P-P1.0-H_WAFER-SH1.0-4PWB
Q1: 8050-Y1; SOT-23
R1: 10M; R_0603_1608Metric
R5, R9, R10: 10K; R_0603_1608Metric
R24: 220R; R_0603_1608Metric
R25: 120R; R_0603_1608Metric
S1, S2: KEY-PB_4P_MIN; KEY-SMD_2P_L4.0-W3.0-V_K2-1807SN-A3DW-06
U2: STM32F103CBTx; LQFP-48_7x7mm_P0.5mm
Y1: 3225 8M 12PF 10PPM; Crystal_SMD_3225-4Pin_3.2x2.5mm

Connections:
+3.3V: J2.4, R5.1, R25.1, U2.1 (VBAT), U2.9 (VDDA), U2.24 (VDD), U2.36 (VDD), U2.48 (VDD); also elsewhere on the board
/CAN_RX: U2.45 (PB8); also elsewhere on the board
/CAN_SILENT: U2.27 (PB14); also elsewhere on the board
/CAN_TX: U2.46 (PB9); also elsewhere on the board
/DEBUG_RX: J1.1, U2.13 (PA3)
/DEBUG_TX: J1.3, U2.12 (PA2)
/KEY1: S1.2, U2.40 (PB4)
/KEY2: S2.2, U2.39 (PB3)
/LED1: R24.2, U2.25 (PB12)
/MT6816_CS: U2.14 (PA4); also elsewhere on the board
/MT6816_MISO: U2.16 (PA6); also elsewhere on the board
/MT6816_MOSI: U2.17 (PA7); also elsewhere on the board
/MT6816_SCK: U2.15 (PA5); also elsewhere on the board
/OSC_IN: C2.1, R1.2, U2.5 (PD0), Y1.1
/OSC_OUT: C6.1, R1.1, U2.6 (PD1), Y1.3
/RS485_DIR: U2.29 (PA8); also elsewhere on the board
/RS485_RX: U2.31 (PA10); also elsewhere on the board
/RS485_TX: U2.30 (PA9); also elsewhere on the board
/SWD_CLK: J2.1, U2.37 (PA14)
/SWD_DIO: J2.2, U2.34 (PA13)
/TB_IN_AM: U2.22 (PB11); also elsewhere on the board
/TB_IN_AP: U2.21 (PB10); also elsewhere on the board
/TB_IN_BM: U2.19 (PB1); also elsewhere on the board
/TB_IN_BP: U2.18 (PB0); also elsewhere on the board
/TB_IN_PWM_A: U2.42 (PB6); also elsewhere on the board
/TB_IN_PWM_B: U2.43 (PB7); also elsewhere on the board
/TB_Temp: U2.11 (PA1); also elsewhere on the board
/nRST: C11.1, R5.2, U2.7 (NRST)
GND: C2.2, C6.2, C11.2, D8.1 (K), J1.2, J2.3, R9.2, R10.2, S1.1, S2.1, U2.8 (VSSA), U2.23 (VSS), U2.35 (VSS), U2.47 (VSS), Y1.2, Y1.4; also elsewhere on the board
unnamed: D8.2 (A), Q1.2 (E)
unnamed: Q1.1 (B), R24.1
unnamed: Q1.3 (C), R25.2
unnamed: R10.1, U2.44 (BOOT0)
unnamed: R9.1, U2.20 (PB2)

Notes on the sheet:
Motor42 Driver Ver 1.0 Designed by Zhbi98
Consult the crystal oscillator data sheet to determine the matching capacitance value,The signal amplitude of the matched capacitance value is typically 100mV-200mV,12pF-20pF
Motor42 Driver

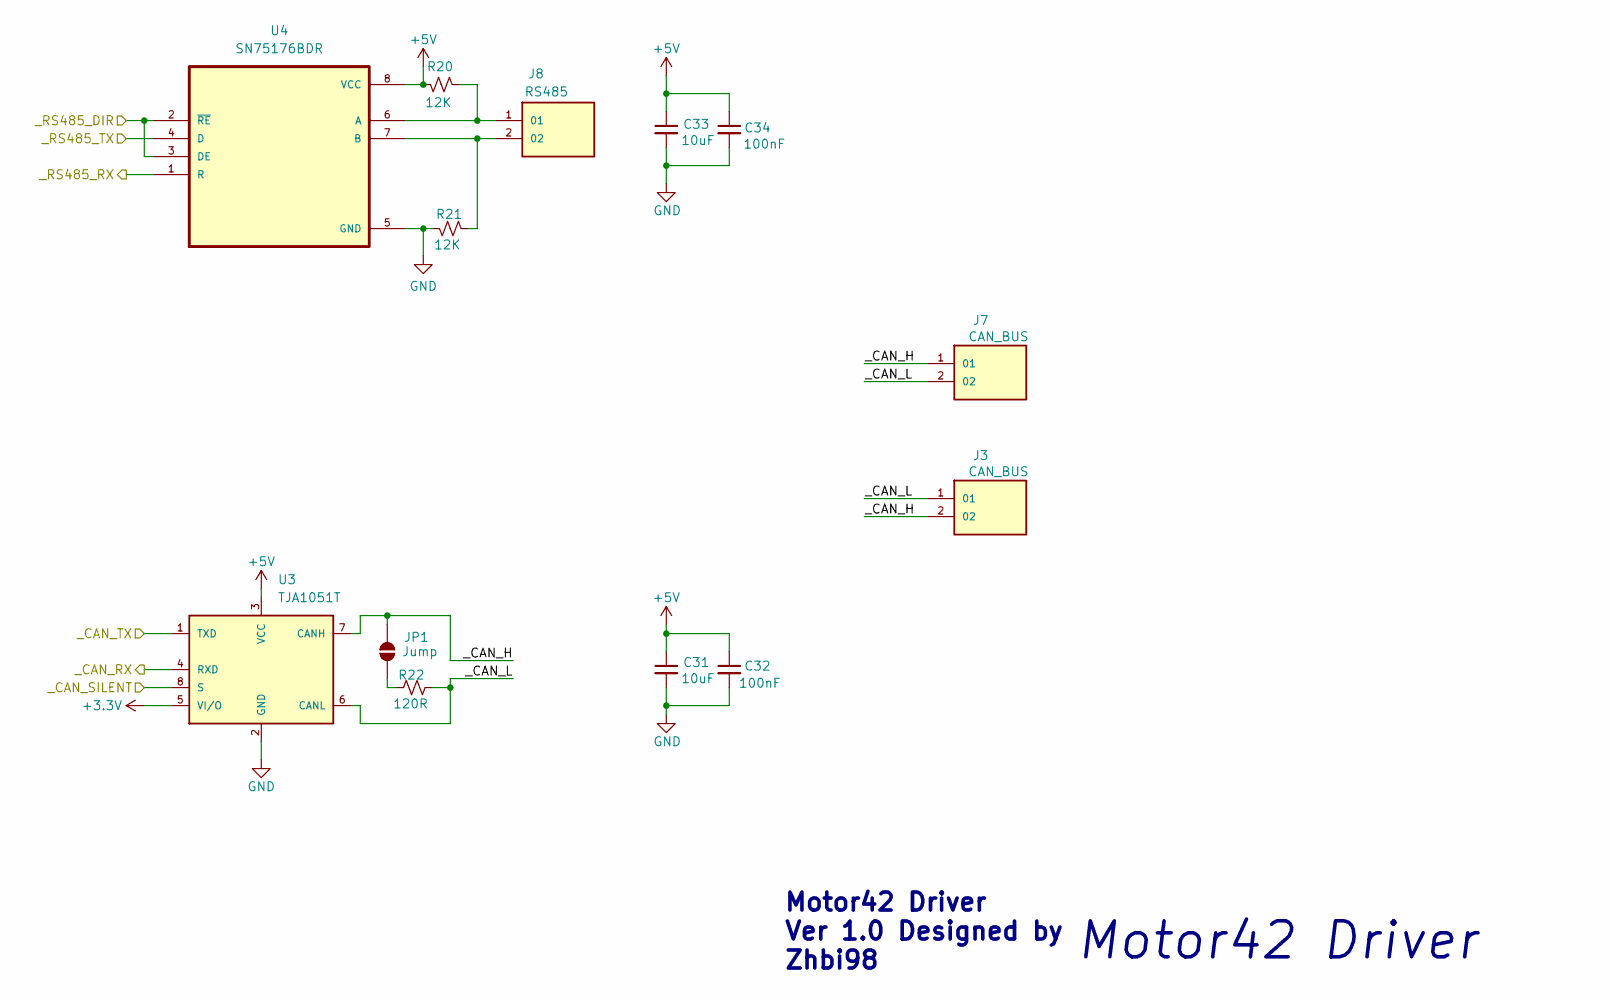
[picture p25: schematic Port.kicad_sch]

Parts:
C31, C33: 10uF; C_0603_1608Metric
C32, C34: 100nF; C_0603_1608Metric
J3, J7: CAN_BUS; CONN-SMD_1x2P-P1.0-H_WAFER-SH1.0-2PWB
J8: RS485; CONN-SMD_1x2P-P1.0-H_WAFER-SH1.0-2PWB
JP1: Jump; SolderJumper-2_P1.3mm_Open_RoundedPad1.0x1.5mm
R20, R21: 12K; R_0603_1608Metric
R22: 120R; R_0603_1608Metric
U3: TJA1051T; SOT96_L5.0-W4.0-P1.27_TJA1051
U4: SN75176BDR; SOIC-8_L5.0-W3.9-P1.27_SN75176BDR

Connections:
+3.3V: U3.5 (VI/O); also elsewhere on the board
+5V: C31.1, C32.1, C33.1, C34.1, R20.1, U3.3 (VCC), U4.8 (VCC); also elsewhere on the board
/CAN_RX: U3.4 (RXD); also elsewhere on the board
/CAN_SILENT: U3.8 (S); also elsewhere on the board
/CAN_TX: U3.1 (TXD); also elsewhere on the board
/PORT/_CAN_H: J3.2, J7.1, JP1.1 (A), U3.7 (CANH)
/PORT/_CAN_L: J3.1, J7.2, R22.2, U3.6 (CANL)
/RS485_DIR: U4.2 (~RE), U4.3 (DE); also elsewhere on the board
/RS485_RX: U4.1 (R); also elsewhere on the board
/RS485_TX: U4.4 (D); also elsewhere on the board
GND: C31.2, C32.2, C33.2, C34.2, R21.1, U3.2 (GND), U4.5 (GND); also elsewhere on the board
unnamed: J8.1, R20.2, U4.6 (A)
unnamed: J8.2, R21.2, U4.7 (B)
unnamed: JP1.2 (B), R22.1

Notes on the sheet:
Motor42 Driver
Motor42 Driver Ver 1.0 Designed by Zhbi98

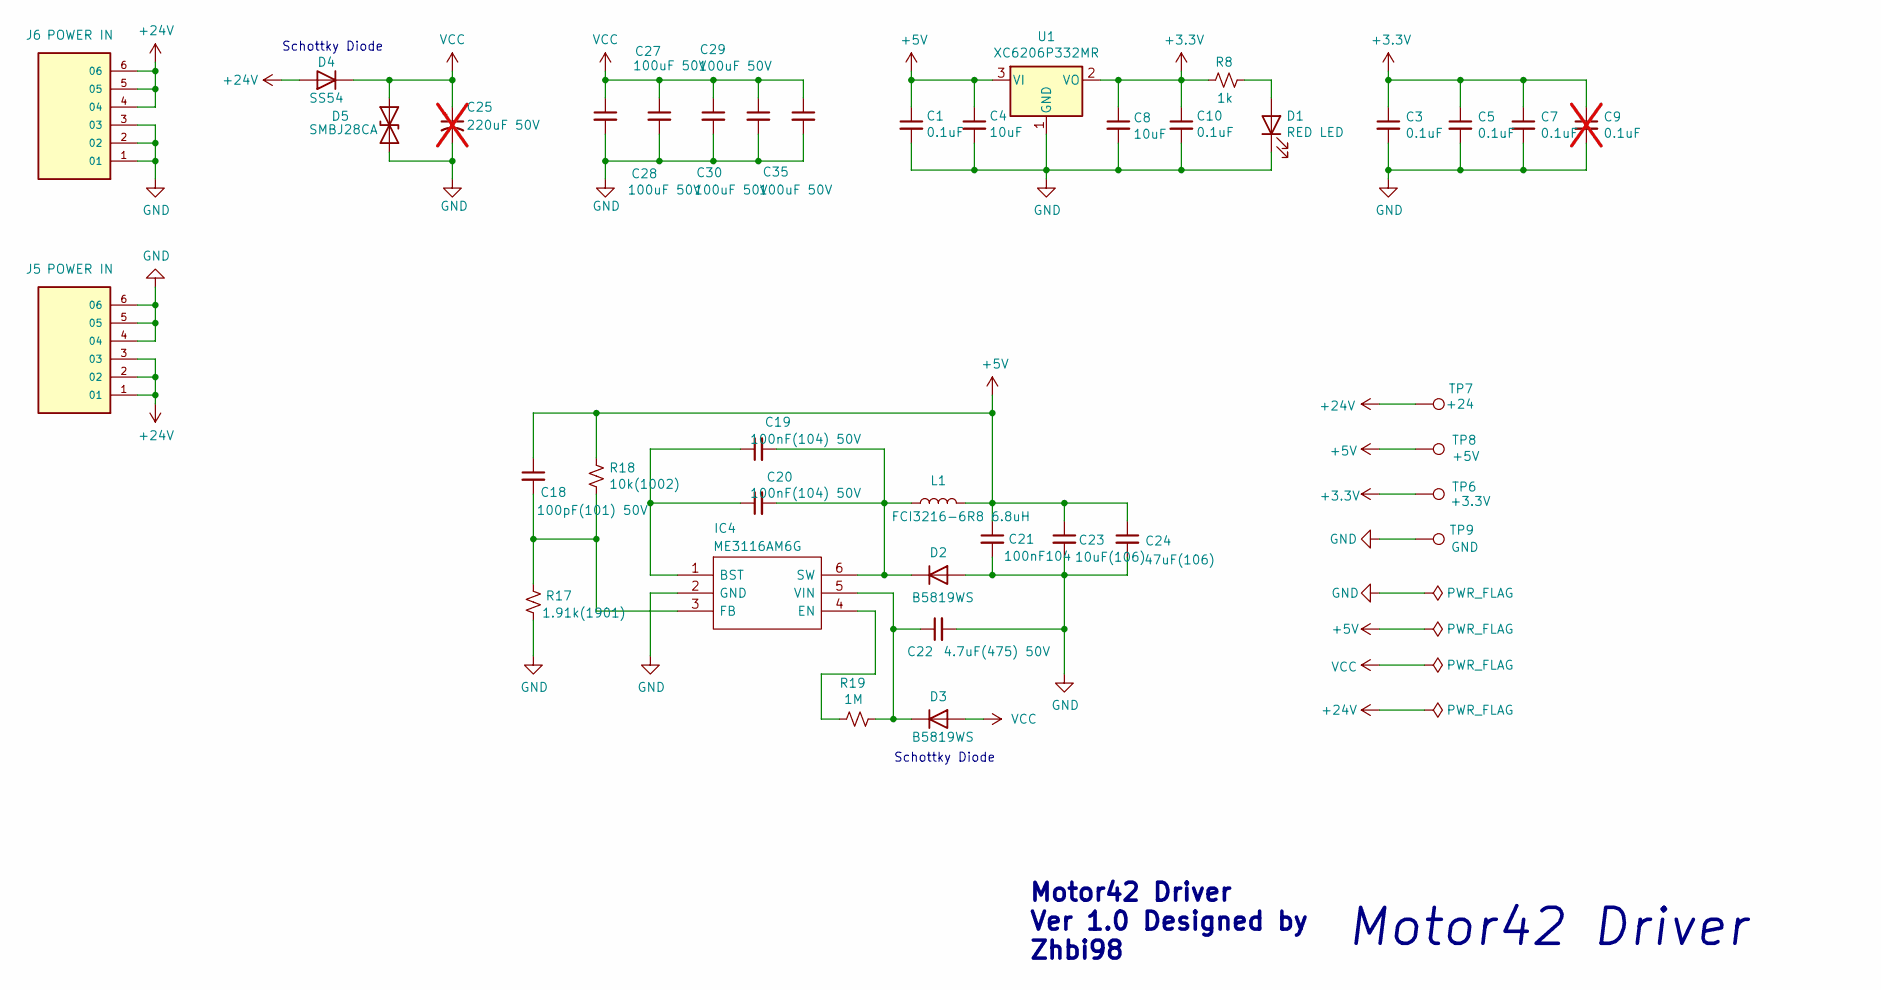
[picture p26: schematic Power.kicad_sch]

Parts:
C1, C3, C5, C7, C10: 0.1uF; C_0603_1608Metric
C4, C8: 10uF; C_0603_1608Metric
C9: 0.1uF; C_0603_1608Metric; not fitted
C18: 100pF(101) 50V; C_0603_1608Metric
C19, C20: 100nF(104) 50V; C_0603_1608Metric
C21: 100nF104; C_0603_1608Metric
C22: 4.7uF(475) 50V; C_1206_3216Metric
C23: 10uF(106); C_0603_1608Metric
C24: 47uF(106); C_0603_1608Metric
C25: 220uF 50V; CP_Elec_4x3; not fitted
C27, C28, C29, C30, C35: 100uF 50V; C_1206_3216Metric
D1: RED LED; LED_0603_1608Metric
D2, D3: B5819WS; D_0805_2012Metric
D4: SS54; D_SMA
D5: SMBJ28CA; D_SMB
IC4: ME3116AM6G; SOT-23-6_L2.7-W2.2-P0.95_ME3116AM6G; Manufacturer_Part_Number ME3116AM6G; Mouser Part Number 946-MP2451DTLFZ
J5, J6: POWER IN; CONN-SMD_1x6P-P2.0-H_WAFER-PH2.0-6PWB
L1: FCI3216-6R8 6.8uH; L_1206_3216Metric
R8: 1k; R_0603_1608Metric
R17: 1.91k(1901); R_0603_1608Metric
R18: 10k(1002); R_0603_1608Metric
R19: 1M; R_0603_1608Metric
TP6: +3.3V; TestPoint_Pad_D1.0mm
TP7: +24; TestPoint_Pad_D1.0mm
TP8: +5V; TestPoint_Pad_D1.0mm
TP9: GND; TestPoint_Pad_D1.0mm
U1: XC6206P332MR; SOT-23

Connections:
+3.3V: C3.1, C5.1, C7.1, C8.1, C9.1, C10.1, R8.1, TP6.1, U1.2 (VO); also elsewhere on the board
+5V: C1.1, C4.1, C18.1, C21.1, C23.1, C24.1, L1.2, R18.1, TP8.1, U1.3 (VI); also elsewhere on the board
+24V: D4.2 (A), J5.1, J5.2, J5.3, J6.4, J6.5, J6.6, TP7.1
GND: C1.2, C3.2, C4.2, C5.2, C7.2, C8.2, C9.2, C10.2, C21.2, C22.2, C23.2, C24.2, C25.2, C27.2, C28.2, C29.2, C30.2, C35.2, D1.1 (K), D2.2 (A), D5.1 (A1), IC4.2 (GND), J5.4, J5.5, J5.6, J6.1, J6.2, J6.3, R17.2, TP9.1, U1.1 (GND); also elsewhere on the board
unnamed: D1.2 (A), R8.2
unnamed: C19.2, C20.2, D2.1 (K), IC4.6 (SW), L1.1
unnamed: C22.1, D3.1 (K), IC4.5 (VIN), R19.2
unnamed: C19.1, C20.1, IC4.1 (BST)
unnamed: IC4.4 (EN), R19.1
unnamed: C18.2, IC4.3 (FB), R17.1, R18.2
VCC: C25.1, C27.1, C28.1, C29.1, C30.1, C35.1, D3.2 (A), D4.1 (K), D5.2 (A2); also elsewhere on the board

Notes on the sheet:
Schottky Diode
Motor42 Driver Ver 1.0 Designed by Zhbi98
Motor42 Driver

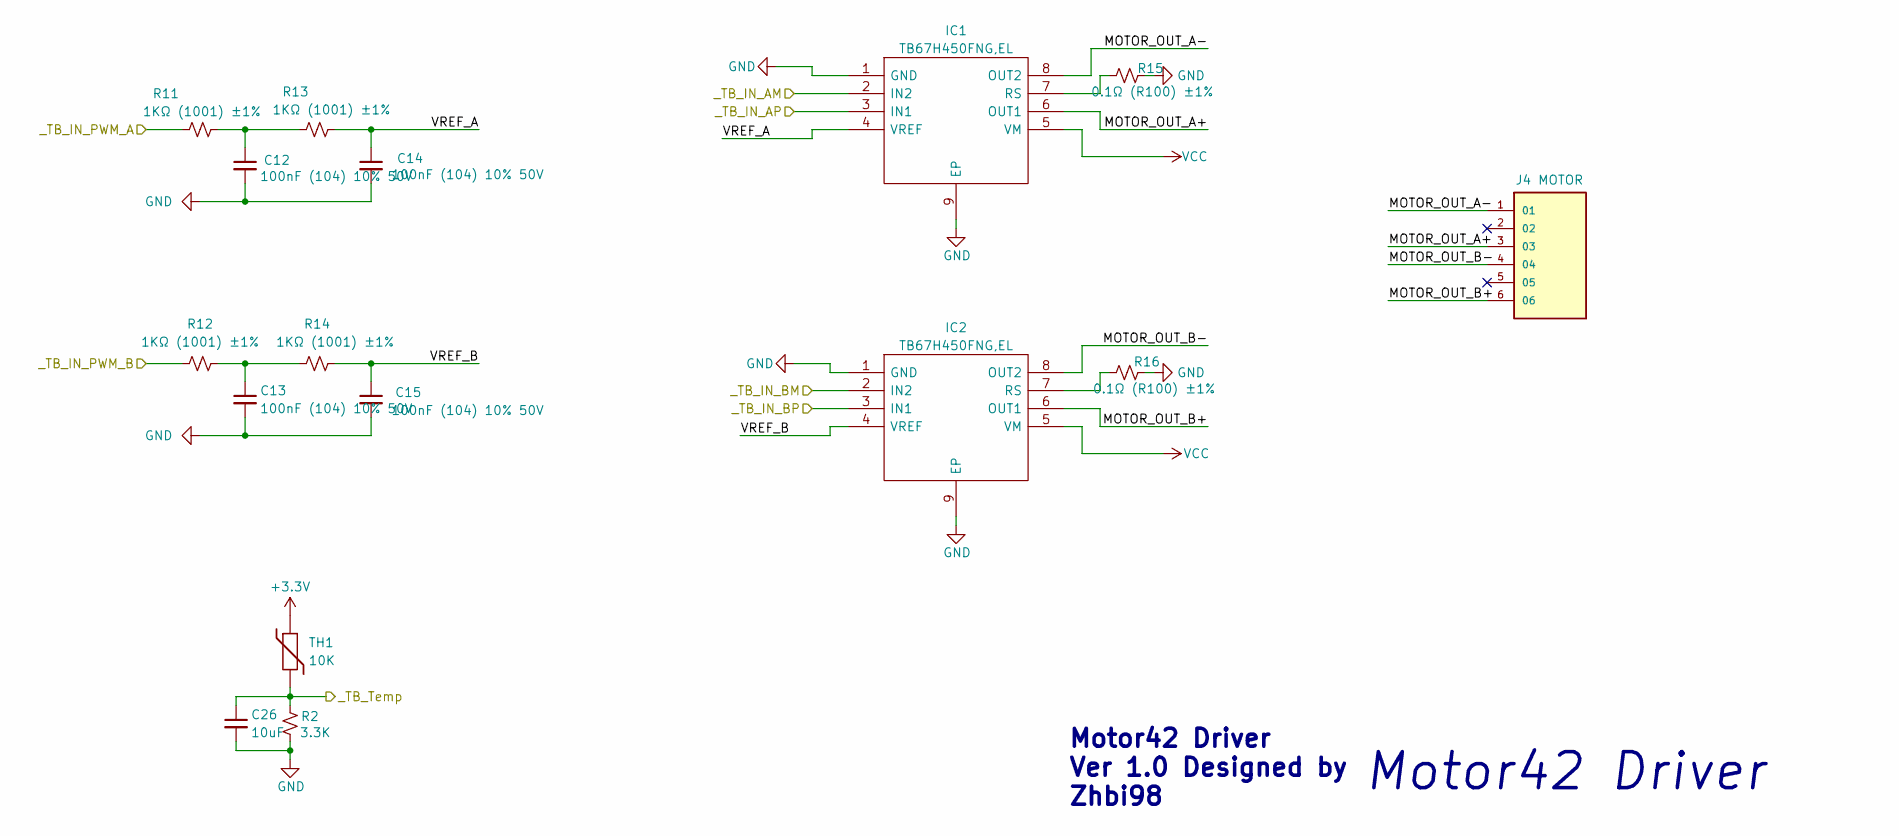
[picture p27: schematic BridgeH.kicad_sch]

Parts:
C12, C13, C14, C15: 100nF (104) 10% 50V; C_0603_1608Metric
C26: 10uF; C_0603_1608Metric
IC1, IC2: TB67H450FNG,EL; SOIC-8_L4.8-W5.8-P1.27_TB67H450FNG; Manufacturer_Part_Number TB67H450FNG,EL; Mouser Part Number 757-TB67H450FNGEL
J4: MOTOR; CONN-SMD_1x6P-P2.0-H_WAFER-PH2.0-6PWB
R2: 3.3K; R_0603_1608Metric
R11, R12, R13, R14: 1KΩ (1001) ±1%; R_0603_1608Metric
R15, R16: 0.1Ω (R100) ±1%; R_1206_3216Metric
TH1: 10K; R_0603_1608Metric

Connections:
+3.3V: TH1.1; also elsewhere on the board
/H_BRID/MOTOR_OUT_A+: IC1.6 (OUT1), J4.3
/H_BRID/MOTOR_OUT_A-: IC1.8 (OUT2), J4.1
/H_BRID/MOTOR_OUT_B+: IC2.6 (OUT1), J4.6
/H_BRID/MOTOR_OUT_B-: IC2.8 (OUT2), J4.4
/H_BRID/VREF_A: C14.1, IC1.4 (VREF), R13.2
/H_BRID/VREF_B: C15.1, IC2.4 (VREF), R14.2
/TB_IN_AM: IC1.2 (IN2); also elsewhere on the board
/TB_IN_AP: IC1.3 (IN1); also elsewhere on the board
/TB_IN_BM: IC2.2 (IN2); also elsewhere on the board
/TB_IN_BP: IC2.3 (IN1); also elsewhere on the board
/TB_IN_PWM_A: R11.1; also elsewhere on the board
/TB_IN_PWM_B: R12.1; also elsewhere on the board
/TB_Temp: C26.1, R2.2, TH1.2; also elsewhere on the board
GND: C12.2, C13.2, C14.2, C15.2, C26.2, IC1.1 (GND), IC1.9 (EP), IC2.1 (GND), IC2.9 (EP), R2.1, R15.2, R16.2; also elsewhere on the board
unnamed: C12.1, R11.2, R13.1
unnamed: C13.1, R12.2, R14.1
unnamed: IC1.7 (RS), R15.1
unnamed: IC2.7 (RS), R16.1
VCC: IC1.5 (VM), IC2.5 (VM); also elsewhere on the board

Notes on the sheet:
Motor42 Driver Ver 1.0 Designed by Zhbi98
Motor42 Driver

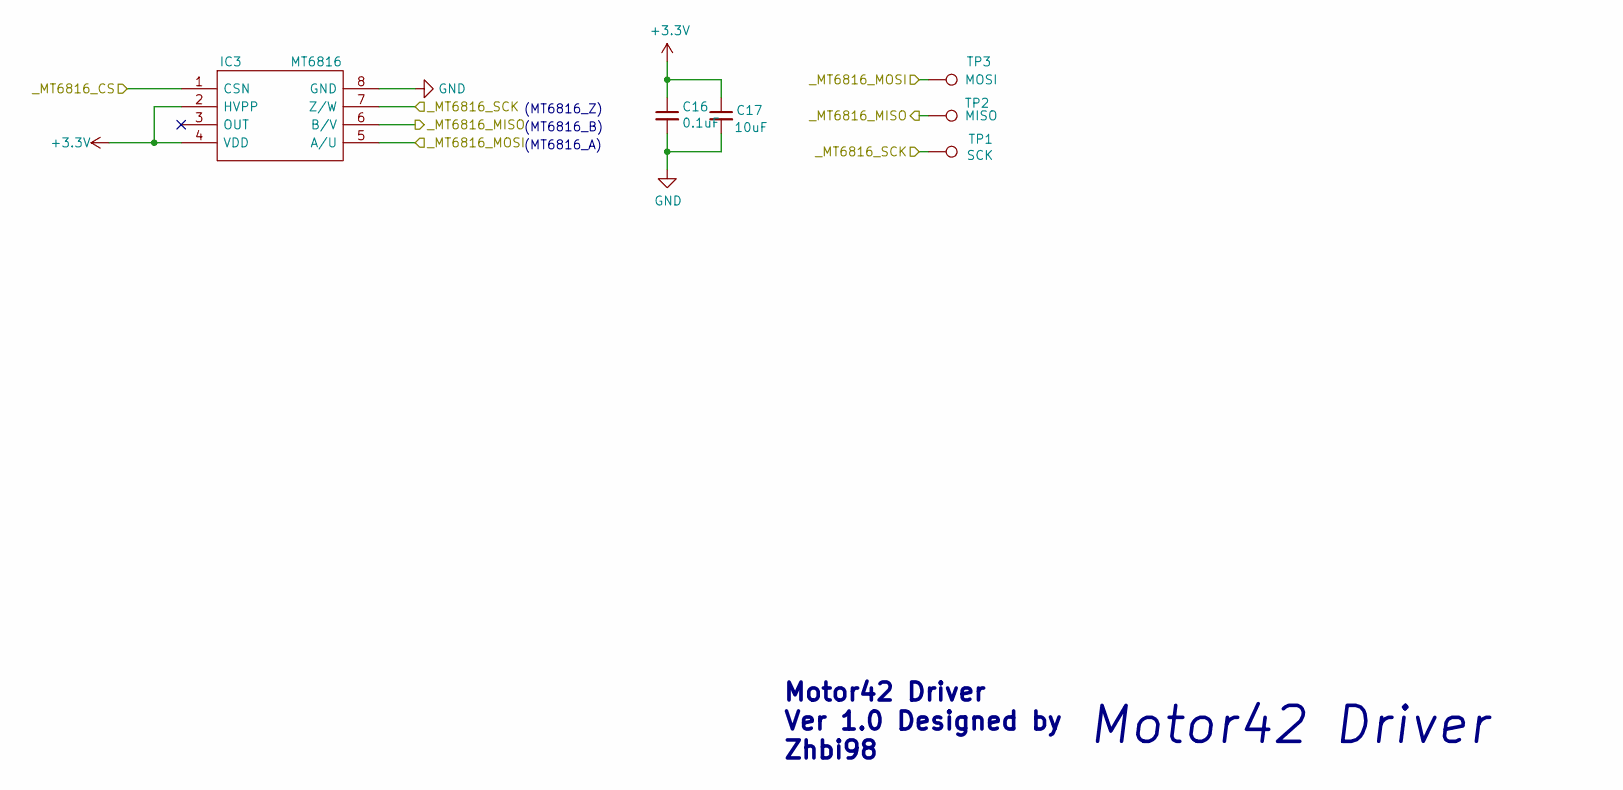
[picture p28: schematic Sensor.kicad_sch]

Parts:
C16: 0.1uF; C_0603_1608Metric
C17: 10uF; C_0603_1608Metric
IC3: MT6816; SOIC-8_L4.7-W5.8-P1.27_MT6816; Manufacturer_Part_Number MT6816
TP1: SCK; TestPoint_Pad_D1.0mm
TP2: MISO; TestPoint_Pad_D1.0mm
TP3: MOSI; TestPoint_Pad_D1.0mm

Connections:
+3.3V: C16.1, C17.1, IC3.2 (HVPP), IC3.4 (VDD); also elsewhere on the board
/MT6816_CS: IC3.1 (CSN); also elsewhere on the board
/MT6816_MISO: IC3.6 (B/V), TP2.1; also elsewhere on the board
/MT6816_MOSI: IC3.5 (A/U), TP3.1; also elsewhere on the board
/MT6816_SCK: IC3.7 (Z/W), TP1.1; also elsewhere on the board
GND: C16.2, C17.2, IC3.8 (GND); also elsewhere on the board

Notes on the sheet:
(MT6816_B)
(MT6816_A)
Motor42 Driver
Motor42 Driver Ver 1.0 Designed by Zhbi98
(MT6816_Z)

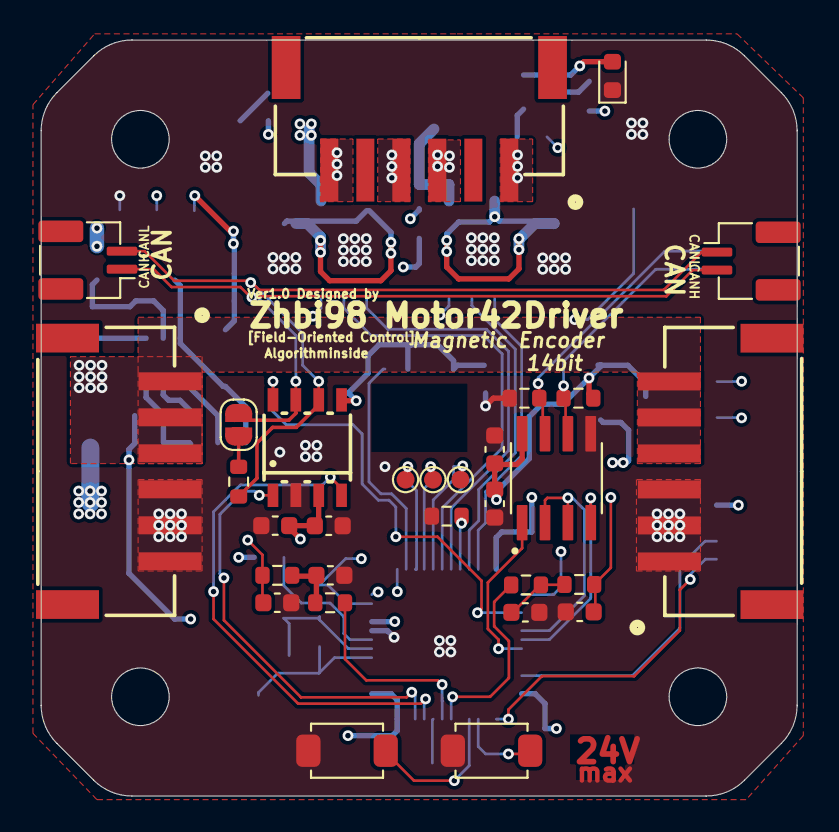
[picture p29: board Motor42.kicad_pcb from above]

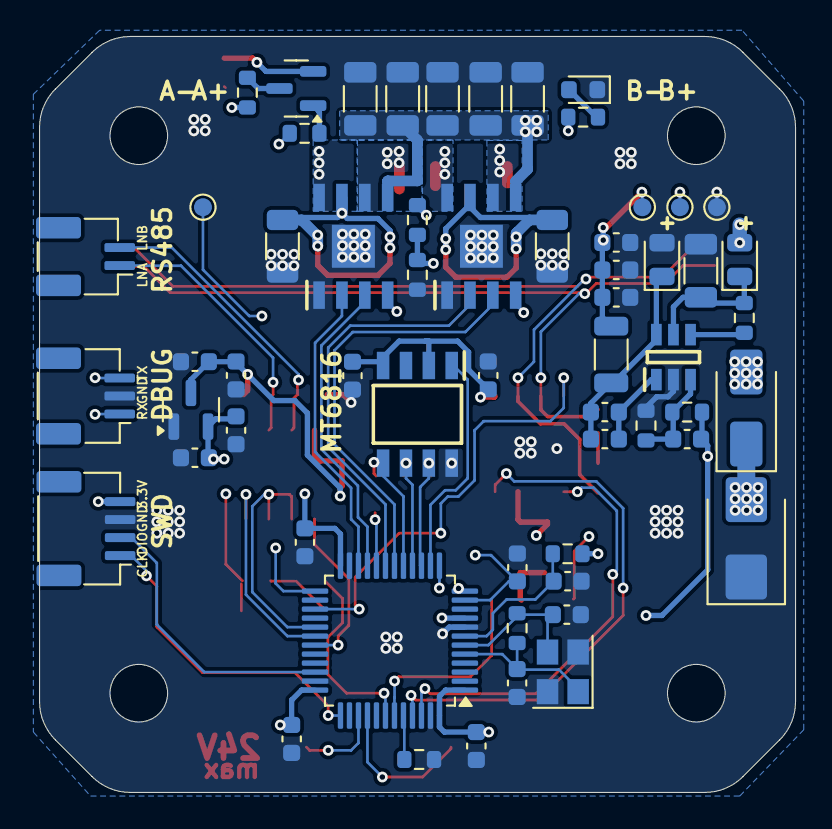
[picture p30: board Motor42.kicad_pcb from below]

Board: 4 copper layers, 42.0 x 42.0 mm, 89 parts (59 on the bottom side), 58 nets.

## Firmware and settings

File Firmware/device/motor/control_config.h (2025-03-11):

/******
	************************************************************************
	******
	** @project : XDrive_Step
	** @brief   : Stepper motor with multi-function interface and closed loop function. 
	** @brief   : 具有多功能接口和闭环功能的步进电机
	** @author  : unlir (知不知啊)
	** @contacts: QQ.1354077136
	******
	** @address : https://github.com/unlir/XDrive
	******
	************************************************************************
	******
	** {Stepper motor with multi-function interface and closed loop function.}
	** Copyright (c) {2020}  {unlir(知不知啊)}
	** 
	** This program is free software: you can redistribute it and/or modify
	** it under the terms of the GNU General Public License as published by
	** the Free Software Foundation, either version 3 of the License, or
	** (at your option) any later version.
	** 
	** This program is distributed in the hope that it will be useful,
	** but WITHOUT ANY WARRANTY; without even the implied warranty of
	** MERCHANTABILITY or FITNESS FOR A PARTICULAR PURPOSE.  See the
	** GNU General Public License for more details.
	** 
	** You should have received a copy of the GNU General Public License
	** along with this program.  If not, see <http://www.gnu.org/licenses/>.
	******
	************************************************************************
******/

/*****
  ** @file     : control_config.c/h
  ** @brief    : 控制配置
  ** @versions : 2.2.3
  ** @time     : 2020/09/15
  ** @reviser  : unli (HeFei China)
  ** @explain  : null
*****/

#ifndef CONTROL_CONFIG_H
#define CONTROL_CONFIG_H

#ifdef __cplusplus
extern "C" {
#endif

#include <stdint.h>
#include <stdbool.h>

/********************  硬件配置区  ********************/
#define _Current_Rated_Current  (3000)  /**< 额定电流(mA)*/
#define _Current_Cali_Current   (2000)  /**< 校准电流(mA)*/

/********************  运动参数配置区  ********************/
#define Move_Step_NUM               ((int32_t)(200))  /**< (使用的电机单圈步数)(每步磁场旋转90°)*/
#define Move_Divide_NUM             ((int32_t)(256))  /**< (每步柔性件控制细分量)*/
#define Move_Pulse_NUM              ((int32_t)(Move_Step_NUM * Move_Divide_NUM))  /**< (电机单圈脉冲数)*/
#define _Move_Rated_Speed           ((int32_t)(50 * Move_Pulse_NUM))    /**< (额定转速)(50转每秒)*/
#define _Move_Rated_UpAcc           ((int32_t)(1000 * Move_Pulse_NUM))  /**< (固件额定加速加速度)(1000r/ss)*/
#define _Move_Rated_DownAcc         ((int32_t)(1000 * Move_Pulse_NUM))  /**(固件额定减速加速度)(1000r/ss)*/
#define _Move_Rated_UpCurrentRate   ((int32_t)(20 * _Current_Rated_Current))	/**< (固件额定增流梯度)(20倍额定/s)*/
#define _Move_Rated_DownCurrentRate	((int32_t)(20 * _Current_Rated_Current))	/**< (固件额定减流梯度)(20倍额定/s)*/

/****************************************  控制器频率配置区  ****************************************/
#define CONTROL_FREQ_HZ   (20000)                     /**< 控制频率_hz*/
#define CONTROL_PERIOD_US (1000000 / CONTROL_FREQ_HZ) /**< 控制周期_us*/

/*void Control_Config_Init_Static(void);  // 控制静态配置*/
/*void Control_Config_Init_Dynamic(void); // 控制动态配置*/

/********************  可变硬件配置区  ************************/
extern int32_t Current_Rated_Current; /**< 额定电流(mA)*/
extern int32_t Current_Cali_Current;  /**< 校准电流(mA)*/

/********************  可变运动参数配置区  ********************/
extern int32_t Move_Home_Offset;
extern int32_t Move_Rated_Speed;           /**< (额定转速)(50转每秒)*/
extern int32_t Move_Rated_UpAcc;           /**< (固件额定加速加速度)(1000r/ss)*/
extern int32_t Move_Rated_DownAcc;         /**< (固件额定减速加速度)(1000r/ss)*/
extern int32_t Move_Rated_UpCurrentRate;   /**< (固件额定增流梯度)(20倍额定/s)*/
extern int32_t Move_Rated_DownCurrentRate; /**< (固件额定减流梯度)(20倍额定/s)*/

#ifdef __cplusplus
}
#endif

#endif

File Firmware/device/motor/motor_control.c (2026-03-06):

/******
	************************************************************************
	******
	** @project : XDrive_Step
	** @brief   : Stepper motor with multi-function interface and closed loop function. 
	** @brief   : 具有多功能接口和闭环功能的步进电机
	** @author  : unlir (知不知啊)
	** @contacts: QQ.1354077136
	******
	** @address : https://github.com/unlir/XDrive
	******
	************************************************************************
	******
	** {Stepper motor with multi-function interface and closed loop function.}
	** Copyright (c) {2020}  {unlir(知不知啊)}
	** 
	** This program is free software: you can redistribute it and/or modify
	** it under the terms of the GNU General Public License as published by
	** the Free Software Foundation, either version 3 of the License, or
	** (at your option) any later version.
	** 
	** This program is distributed in the hope that it will be useful,
	** but WITHOUT ANY WARRANTY; without even the implied warranty of
	** MERCHANTABILITY or FITNESS FOR A PARTICULAR PURPOSE.  See the
	** GNU General Public License for more details.
	** 
	** You should have received a copy of the GNU General Public License
	** along with this program.  If not, see <http://www.gnu.org/licenses/>.
	******
	************************************************************************
******/

/*****
  ** @file     : control_config.c/h
  ** @brief    : 电机控制
  ** @versions : 2.2.3
  ** @time     : 2020/09/15
  ** @reviser  : unli (HeFei China)
  ** @explain  : null
*****/

/*Oneself*/
#include "motor_control.h"

/*Base_Drivers*/
#include "mt6816.h"
#include "tb67h450.h"/*#include "hw_elec.h"*/
/*#include "signal_port.h"*/
#include "enc_cali.h"
#include "temp.h"

/*Control*/
#include "control_config.h"
#include "Location_Tracker.h"
#include "Speed_Tracker.h"
#include "Current_Tracker.h"
#include "Move_Reconstruct.h"
#include "Location_Interp.h"

/****************************************  电流输出(电流控制)  ****************************************/
/****************************************  电流输出(电流控制)  ****************************************/
/**
  * @brief  电流输出
  * @param  current: 输出电流
  * @retval NULL
**/
void Control_Cur_To_Electric(int16_t current)
{
	//输出FOC电流
	motor_control.foc_current = current;
	//输出FOC位置
	if(motor_control.foc_current > 0)				motor_control.foc_location = motor_control.est_location + Move_Divide_NUM;
	else if(motor_control.foc_current < 0)	motor_control.foc_location = motor_control.est_location - Move_Divide_NUM;
	else																		motor_control.foc_location = motor_control.est_location;
	//输出任务到驱动
	tb_foc_set_current_vector(motor_control.foc_location, motor_control.foc_current);
	//CurrentControl_Out_FeedTrack(motor_control.foc_location, motor_control.foc_current, false, true);
}

/****************************************  PID控制(速度控制)  ****************************************/
/****************************************  PID控制(速度控制)  ****************************************/
//PID控制
Control_PID_Typedef pid;

/**
  * @brief  参数配置
  * @param  _k
  * @retval NULL
**/
void Control_PID_SetKP(uint16_t _k)
{
	if(_k <= 1024){		pid.kp = _k;		pid.valid_kp = true;		}
	else{															pid.valid_kp = false;		}
}

/**
  * @brief  参数配置
  * @param  _k
  * @retval NULL
**/
void Control_PID_SetKI(uint16_t _k)
{
	if(_k <= 1024){		pid.ki = _k;		pid.valid_ki = true;		}
	else{															pid.valid_ki = false;		}
}

/**
  * @brief  参数配置
  * @param  _k
  * @retval NULL
**/
void Control_PID_SetKD(uint16_t _k)
{
	if(_k <= 1024){		pid.kd = _k;		pid.valid_kd = true;		}
	else{															pid.valid_kd = false;		}
}

/**
  * @brief  PID参数恢复
  * @param  NULL
  * @retval NULL
**/
void Control_PID_Set_Default(void)
{
	Control_PID_SetKP(De_PID_KP);
	Control_PID_SetKI(De_PID_KI);
	Control_PID_SetKD(De_PID_KD);
}

/**
  * @brief  控制器PID初始化
  * @param  NULL
  * @retval NULL
**/
void Control_PID_Init(void)
{
	//前置配置无效时,加载默认配置
	if(!pid.valid_kp)				{	Control_PID_SetKP(De_PID_KP);		}
	if(!pid.valid_ki)				{	Control_PID_SetKI(De_PID_KI);		}
	if(!pid.valid_kd)				{	Control_PID_SetKD(De_PID_KD);		}
	
	//控制参数
	pid.v_error = 0;	pid.v_error_last = 0;
	pid.op = 0;				pid.oi = 0;			pid.od = 0;	
	pid.i_mut = 0;		pid.i_dec = 0;
	pid.out = 0;
}

/**
  * @brief  PID电流控制
  * @param  _speed    控制速度
  * @retval NULL
**/
void Control_PID_To_Electric(int32_t _speed)
{
	//误差
	pid.v_error_last = pid.v_error;
	pid.v_error = _speed - motor_control.est_speed;	//速度误差
	if(pid.v_error > ( 1024 * 1024))	pid.v_error = ( 1024 * 1024);
	if(pid.v_error < (-1024 * 1024))	pid.v_error = (-1024 * 1024);
	//op输出（比例项）
	pid.op = ((pid.kp) * (pid.v_error));
	//oi输出（积分项，速度误差的积分，通过累加实现，
	//通过右移操作进行衰减，防止积分饱和）
	pid.i_mut += ((pid.ki) * (pid.v_error));
	pid.i_dec  = (pid.i_mut >> 10);
	pid.i_mut -= (pid.i_dec << 10);
	pid.oi    += (pid.i_dec);
	if(pid.oi >      (  Current_Rated_Current << 10 ))	pid.oi = (  Current_Rated_Current << 10 );	//限制为额定电流 * 1024
	else if(pid.oi < (-(Current_Rated_Current << 10)))	pid.oi = (-(Current_Rated_Current << 10));	//限制为额定电流 * 1024
	//od输出（微分项，注意将微分项应用于速度误差的差值)
	pid.od = (pid.kd) * (pid.v_error - pid.v_error_last);
	//综合输出计算（同时限制输出范围，限制最终输出电流在额定电流范围内）
	pid.out = (pid.op + pid.oi + pid.od) >> 10;
	if(pid.out > 			Current_Rated_Current)		pid.out =  Current_Rated_Current;
	else if(pid.out < -Current_Rated_Current)		pid.out = -Current_Rated_Current;
	
	//输出FOC电流
	motor_control.foc_current = pid.out;
	//输出FOC位置
	if(motor_control.foc_current > 0)				motor_control.foc_location = motor_control.est_location + Move_Divide_NUM;
	else if(motor_control.foc_current < 0)	motor_control.foc_location = motor_control.est_location - Move_Divide_NUM;
	else																		motor_control.foc_location = motor_control.est_location;
	//输出任务到驱动
	tb_foc_set_current_vector(motor_control.foc_location, motor_control.foc_current);
	//CurrentControl_Out_FeedTrack(motor_control.foc_location, motor_control.foc_current, false, true);
}

/****************************************  DCE控制器(位置控制)  ****************************************/
/****************************************  DCE控制器(位置控制)  ****************************************/
//DCE控制
Control_DCE_Typedef dce;

/**
  * @brief  参数配置
  * @param  _k
  * @retval NULL
**/
void Control_DCE_SetKP(uint16_t _k)
{
	if(_k <= 1024){		dce.kp = _k;		dce.valid_kp = true;		}
	else{															dce.valid_kp = false;		}
}

/**
  * @brief  参数配置
  * @param  _k
  * @retval NULL
**/
void Control_DCE_SetKI(uint16_t _k)
{
	if(_k <= 1024){		dce.ki = _k;		dce.valid_ki = true;		}
	else{															dce.valid_ki = false;		}
}

/**
  * @brief  参数配置
  * @param  _k
  * @retval NULL
**/
void Control_DCE_SetKV(uint16_t _k)
{
	if(_k <= 1024){		dce.kv = _k;		dce.valid_kv = true;		}
	else{															dce.valid_kv = false;		}
}

/**
  * @brief  参数配置
  * @param  _k
  * @retval NULL
**/
void Control_DCE_SetKD(uint16_t _k)
{
	if(_k <= 1024){		dce.kd = _k;		dce.valid_kd = true;		}
	else{															dce.valid_kd = false;		}
}
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

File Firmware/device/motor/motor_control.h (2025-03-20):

/******
	************************************************************************
	******
	** @project : XDrive_Step
	** @brief   : Stepper motor with multi-function interface and closed loop function. 
	** @brief   : 具有多功能接口和闭环功能的步进电机
	** @author  : unlir (知不知啊)
	** @contacts: QQ.1354077136
	******
	** @address : https://github.com/unlir/XDrive
	******
	************************************************************************
	******
	** {Stepper motor with multi-function interface and closed loop function.}
	** Copyright (c) {2020}  {unlir(知不知啊)}
	** 
	** This program is free software: you can redistribute it and/or modify
	** it under the terms of the GNU General Public License as published by
	** the Free Software Foundation, either version 3 of the License, or
	** (at your option) any later version.
	** 
	** This program is distributed in the hope that it will be useful,
	** but WITHOUT ANY WARRANTY; without even the implied warranty of
	** MERCHANTABILITY or FITNESS FOR A PARTICULAR PURPOSE.  See the
	** GNU General Public License for more details.
	** 
	** You should have received a copy of the GNU General Public License
	** along with this program.  If not, see <http://www.gnu.org/licenses/>.
	******
	************************************************************************
******/

/*****
  ** @file     : control_config.c/h
  ** @brief    : 电机控制
  ** @versions : 2.2.3
  ** @time     : 2020/09/15
  ** @reviser  : unli (HeFei China)
  ** @explain  : null
*****/

#ifndef MOTOR_CONTROL_H
#define MOTOR_CONTROL_H

#ifdef __cplusplus
extern "C" {
#endif

//引用端口定义
/*#include "kernel_port.h", Modify by zhbi98*/
#include <stdbool.h>
#include <stdint.h>
#include <stdlib.h>

/****************************************  直接控制(电流控制)  ****************************************/
/****************************************  直接控制(电流控制)  ****************************************/
void Control_Cur_To_Electric(int16_t current);		//电流输出

/****************************************  PID控制(速度控制)  ****************************************/
/****************************************  PID控制(速度控制)  ****************************************/
typedef struct{
	//配置
	#define De_PID_KP	5		//默认KP
	#define De_PID_KI	30	//默认KI
	#define De_PID_KD	0		//默认KD
	bool		valid_kp, valid_ki, valid_kd;	//参数有效标志
	int32_t	kp, ki, kd;		//参数
	//控制参数
	int32_t		v_error, v_error_last;	//误差记录
	int32_t		op, oi, od;							//输出
	int32_t		i_mut, i_dec;						//小积分处理
	int32_t		out;										//输出
}Control_PID_Typedef;
extern Control_PID_Typedef pid;

//参数配置
void Control_PID_SetKP(uint16_t _k);		//KP参数配置
void Control_PID_SetKI(uint16_t _k);		//KI参数配置
void Control_PID_SetKD(uint16_t _k);		//KD参数配置
void Control_PID_Set_Default(void);			//PID参数恢复
//初始化
void Control_PID_Init(void);
void Control_PID_To_Electric(int32_t _speed);

/****************************************  DCE控制(位置控制)  ****************************************/
/****************************************  DCE控制(位置控制)  ****************************************/
typedef struct{
	//配置
	#define De_DCE_KP	200		//默认KP
	#define De_DCE_KI	80		//默认KI
	#define De_DCE_KV	300		//默认KIV
	#define De_DCE_KD	250		//默认KD
	bool		valid_kp, valid_ki, valid_kv, valid_kd;	//参数有效标志
	int32_t	kp, ki, kv, kd;		//参数
	//控制参数(基本部分)
	int32_t		p_error, v_error;		//误差记录
	int32_t		op, oi, od;					//输出
	int32_t		i_mut, i_dec;				//小积分处理
	int32_t		out;								//输出
}Control_DCE_Typedef;
extern Control_DCE_Typedef dce;

//参数配置
void Control_DCE_SetKP(uint16_t _k);		//KP参数配置
void Control_DCE_SetKI(uint16_t _k);		//KI参数配置
void Control_DCE_SetKV(uint16_t _k);		//KV参数配置
void Control_DCE_SetKD(uint16_t _k);		//KD参数配置
void Control_DCE_Set_Default(void);			//DCE参数恢复
//初始化
void Control_DCE_Init(void);
void Control_DCE_To_Electric(int32_t _location, int32_t _speed);

/****************************************  Motor_Contro_Debug  ****************************************/
/****************************************  Motor_Contro_Debug  ****************************************/
/**
  * Motor_Control类结构体定义
**/
typedef struct{
	//公共调试
	int32_t		mut;		//调试位置
	int32_t		dec;		//调试位置
	int32_t		speed;	//调试速度
}Motor_Control_Debug_Typedef;
extern Motor_Control_Debug_Typedef mc_debug;

//调试
void Motor_MultiDebug_Location(void);	//多功能调试位置
void Motor_MultiDebug_Speed(void);		//多功能调试速度

/****************************************  Motor_Control  ****************************************/
/****************************************  Motor_Control  ****************************************/
/**
  * 控制器状态
**/
typedef enum{
	Control_State_Stop				= 0x00,	//停止
	Control_State_Finish			= 0x01,	//任务完成
	Control_State_Running			= 0x02,	//任务执行中
	Control_State_Overload		= 0x03,	//过载
	Control_State_Stall				= 0x04,	//堵转
	Control_State_Overtemp		= 0x05,	//过热
}Motor_State;

/**
  * 模式
**/
typedef enum{
	/*****************************************************外部输入量***********信号发生器(可控的运动参数)**开放状态(开放版本)*****/
	//测试
	Motor_Mode_Debug_Location		= 0x00,	//调试位置				NULL									多功能调试信号源						测试版本完整代码
	Motor_Mode_Debug_Speed			= 0x01,	//调试速度				NULL									多功能调试信号源						测试版本完整代码
	//停止
	Control_Mode_Stop						= 0x10,	//停止						NULL									NULL												NULL
	//DIG(CAN/RS485)
	Motor_Mode_Digital_Location	= 0x20,	//DIG位置					目标位置							位置跟踪器(速度,双加速度)		源码开放(20191101)
	Motor_Mode_Digital_Speed		= 0x21,	//DIG速度					目标速度							速度跟踪器(双加速度)				源码开放(20191101)
	Motor_Mode_Digital_Current	= 0x22,	//DIG电流					目标电流							电流跟踪器(双电梯度)				源码开放(20191101)
	Motor_Mode_Digital_Track		= 0x23,	//DIG轨迹					多指令								运动重构器(运动自寻)				源码开放(20191101)
	//MoreIO(PWM/PUL)
	Motor_Mode_PWM_Location			= 0x30,	//PWM位置_舵机		目标位置							位置跟踪器(速度,双加速度)		源码开放(20191101)
	Motor_Mode_PWM_Speed				= 0x31,	//PWM速度_调速机	目标速度							速度跟踪器(双加速度)				源码开放(20191101)
	Motor_Mode_PWM_Current			= 0x32,	//PWM电流_直流机	目标电流							电流跟踪器(双电梯度)				源码开放(20191101)
	Motor_Mode_PULSE_Location		= 0x33,	//PULSE位置				目标位置							位置插补器(无)							源码开放(20200803)
	//Action
	Motor_Mode_QCode						= 0x40,	//Q指令						NULL									任意												内部测试()
	//Demos
	Motor_Mode_Music						= 0x50,	//音乐						NULL									NULL												内部测试()
}Motor_Mode;
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

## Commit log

2025-02-23 更新LED及按键驱动程序
2025-02-23 修改CMakeLists.txt构建目录
2025-02-24 更新文件之间引用关系
2025-02-26 更新 Signal 组件
2025-03-01 添加电机按键控制，与指示灯信号
2025-03-07 添加电机模式按键控制
2025-03-08 添加 CAN 控制指令，增加控制参数请求接口
2025-03-09 用户设置参数存储功能
2025-03-10 完善控制指令，增加磁编码器零点偏移设置
2025-03-11 调整电机可变参数配置与初始化方式
2025-03-13 添加过温保护 ADC 驱动
2025-03-15 解决闭环控制高频中断导致主循环不运行问题(按键, LED不响应)，适配新PCB调整 GPIO 分配
    [btn_doing.c, gpio.c, led_anim.c]
2025-03-16 使用软件定时器解决闭环控制高频中断导致主循环不运行，CAN 中断低优先级中断滞后问题(以及按键, LED不响应)
2025-03-19 复杂计算部分添加注释
2025-03-19 添加硬件设计文档
    [BOM.dxf, BridgeH.kicad_sch, EDG.dxf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]
2025-03-20 添加电机过热检测和保护
2025-03-27 更新震动问题的原因和解决办法说明
2025-04-09 添加 RS485 控制协议
2025-04-14 位置环控制时调节到达目标位置的额定速度和时间，新额定速度，过程时间未生效问题
2025-04-18 添加控制协议表格
    [Protocols-CAN.xlsx, Protocols-RS485.xlsx]
2025-04-19 更新 README,添加零件，添加协议文档
    [Motor42-BOM.csv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]
2025-07-20 Can not set the acceleration, otherwise the mode switching speed can not be limited in time.
    Can not set the acceleration, otherwise the mode switching speed can not be limited in time.
2025-08-12 增加设备串口输出流__fputs接口
2026-03-06 完善README说明文档
